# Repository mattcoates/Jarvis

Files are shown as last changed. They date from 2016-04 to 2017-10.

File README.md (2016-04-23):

#Jarvis Flight Computer & Ground Station

Jarvis is a generic rocket flight computer and ground station for use in my level 1 & 2 certification attempt rockets.

Flight Computer Specifications:
- Size: 30mm x 55mm
- Processor: STM32F411CEU6
- Power Supply: x1 Energizer L91 (AA) w/ Boost Coverter to 3.3v
- Barometer: MS5611
- Pyro Channels: x3 w/ Fire & Sense Functioniality
- Storage: S25FL127S 16MB Flash Memory
- IMU: MPU9250
- GPS: uBlox MAX-M8Q w/ PCB Mount Helical Antenna
- Telemetry: Si4460 Radio Downlink w/ SMA Connector

Ground Station Specifications:
- Size: 16mm x 44mm Dongle
- Processor: STM32F042F6P6
- Power Supply: USB with ADP3335 Regulator
- Telemetry: Si4460 Radio Downlink w/ SMA Connector
- Connectors: USB-A Male Plug

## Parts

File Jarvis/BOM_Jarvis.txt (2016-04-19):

Bill Of Materials
=================

Source file: Jarvis.xml
Date: 2016-04-19T19:52:06.596366

Parts Missing Footprints
------------------------
X1     434MHz ANT     
X5     ARM Switch     
X2     Red LED        
X4     AA Holder      
X3     AA Battery     
X8     Housing x1     
X9     Housing x4     
X10    Housing x1     
X13    F Crimps x17   
X6     Wire           
X14    Crimp Tool     
X12    M Crimps x6    
X7     Heat Shrink    
X11    Housing x3     
X16    RF Cover       

Parts Missing Order Codes
-------------------------
P3     SWD_TC          agg:TC2030-NL
X13    F Crimps x17    None
X6     Wire            None
X12    M Crimps x6     None
X7     Heat Shrink     None
TP19   TESTPAD         agg:TESTPAD
TP15   TESTPAD         agg:TESTPAD
TP6    TESTPAD         agg:TESTPAD
TP11   TESTPAD         agg:TESTPAD
TP4    TESTPAD         agg:TESTPAD
TP10   TESTPAD         agg:TESTPAD
TP12   TESTPAD         agg:TESTPAD
TP7    TESTPAD         agg:TESTPAD
TP1    TESTPAD         agg:TESTPAD
TP16   TESTPAD         agg:TESTPAD
TP14   TESTPAD         agg:TESTPAD
TP9    TESTPAD         agg:TESTPAD
TP3    TESTPAD         agg:TESTPAD
TP18   TESTPAD         agg:TESTPAD
TP13   TESTPAD         agg:TESTPAD
TP8    TESTPAD         agg:TESTPAD
TP2    TESTPAD         agg:TESTPAD
TP17   TESTPAD         agg:TESTPAD
TP26   TESTPAD         agg:TESTPAD
TP25   TESTPAD         agg:TESTPAD
TP24   TESTPAD         agg:TESTPAD
TP20   TESTPAD         agg:TESTPAD
TP21   TESTPAD         agg:TESTPAD
TP22   TESTPAD         agg:TESTPAD
TP38   TESTPAD         agg:TESTPAD
TP40   TESTPAD         agg:TESTPAD
TP33   TESTPAD         agg:TESTPAD
TP37   TESTPAD         agg:TESTPAD
TP39   TESTPAD         agg:TESTPAD
TP36   TESTPAD         agg:TESTPAD
TP44   TESTPAD         agg:TESTPAD
TP45   TESTPAD         agg:TESTPAD
TP41   TESTPAD         agg:TESTPAD
TP42   TESTPAD         agg:TESTPAD
TP47   TESTPAD         agg:TESTPAD
TP48   TESTPAD         agg:TESTPAD
TP43   TESTPAD         agg:TESTPAD
TP23   TESTPAD         agg:TESTPAD
TP32   TESTPAD         agg:TESTPAD
TP30   TESTPAD         agg:TESTPAD
TP31   TESTPAD         agg:TESTPAD
TP28   TESTPAD         agg:TESTPAD
TP27   TESTPAD         agg:TESTPAD
TP29   TESTPAD         agg:TESTPAD
TP35   TESTPAD         agg:TESTPAD
TP46   TESTPAD         agg:TESTPAD
TP34   TESTPAD         agg:TESTPAD
TP5    TESTPAD         agg:TESTPAD
TP49   TESTPAD         agg:TESTPAD

Inconsistent Order Codes
------------------------

Vendor Specific BOMs
--------------------
  RS
  ~~
883-7942,1,,1x--MPU-9250--QFN-24-MPU9250--IC3

  Digikey
  ~~~~~~~
1,AI-1027-TWT-3V-R,1x SOUNDER AI-1027-TWT-3V-R LS1

  Farnell
  ~~~~~~~
2524673,1,1x 10nF 0402-L
2346896,1,1x 2.2uF 0603-L
2455292,1,1x 2.2uH Neosid_Inductor_SM-NE
2310320,2,2x 8.2pF 0402-L
1760988,2,2x 18nH 0402-L
2497715,1,1x RF Frame BMI-S-201-F
2497714,1,1x RF Cover None
1226390,1,1x LED 0603-LED
1830730,1,1x Housing x1 None
2072516,5,5x 1k 0402-L
2072517,16,16x 10k 0402-L
1568023,1,1x MICROUSB MICROUSB_MOLEX_475
1830751,1,1x PYRO S06B-PASK-2
1515785 ,2,2x 1.25R 0402-L
2254940,1,1x ADP1607 LFCSP-2x2
2496792,1,1x 100pF 0402-L
2112849,1,1x 1uF 0603-L
1669639,3,3x 56nH 0402-L
1510761 ,4,4x NFET SOT-23
1894738,3,3x PFET SOT-23
1759381,1,1x 1uF 0402-L
2331061,1,1x 243k 0603-L
1226372,3,3x LED 0603-LED
2293260 ,1,1x AA Holder None
1657936,2,2x 10uF 0805
1863178,1,1x Red LED None
1830747,1,1x PWR S02B-PASK-2
1828860,18,18x 100nF 0402-L
1830726,1,1x Housing x4 None
1758939,2,2x 8pF 0402-L
1830728,1,1x Housing x1 None
1973025,1,1x 15pF 0402-L
1830748,1,1x ARM S03B-PASK-2
1608592,1,1x SMA SMA-142-0701-801
2362662,1,1x MS5611-01BA03 MS5611
1885342,1,1x 18pF 0402-L
2462635,1,1x Si4460 QFN-20-EP-SI
1469661,1,1x 0R 0402-L
1830756 ,1,1x Housing x3 None
2328003,1,1x S25FL127S WND008
2506973,1,1x 30MHz XTAL-20x16
2496800,1,1x 220pF 0402-L
1358015,10,10x 100R 0402-L
2456965,1,1x STM32F411CxUx QFN-48-EP-ST
1885321,1,1x 5.1pF 0402-L
2506952,1,1x 26MHz XTAL-20x16
2426952,2,2x 4.7uF 0402-L
2368169,8,8x ESD_DIODE 0402-L
2310308,1,1x 2.7pF 0402-L
2215631,1,1x 220nH 0603-L
1735379,1,1x ARM Switch None
2483918 ,1,1x 330k 0603-L

  eBay
  ~~~~
http://tinyurl.com/zxwhzow,1,1x X3 None
http://tinyurl.com/jokv8kj,1,1x X14 None

  HabSupplies
  ~~~~~~~~~~~
HAB-434STUB,1,1x X1 None
HAB-MAX-M8Q,1,1x IC2 MAX-7Q
HAB-SL1252R,1,1x P1 SMA-142-0701-801

Assembly BOM
------------
883-7942             1   MPU-9250        QFN-24-MPU9250  IC3
AI-1027-TWT-3V-R     1   SOUNDER         AI-1027-TWT-3V-R LS1
2524673              1   10nF            0402-L          C11
2346896              1   2.2uF           0603-L          C32
2455292              1   2.2uH           Neosid_Inductor_SM-NE29_SMD1008 L1
2310320              2   8.2pF           0402-L          C26 C28
1760988              2   18nH            0402-L          L4 L5
2497715              1   RF Frame        BMI-S-201-F     X15
2497714              1   RF Cover        None            X16
1226390              1   LED             0603-LED        D4
1830730              1   Housing x1      None            X10
2072516              5   1k              0402-L          R21 R22 R23 R24 R25
2072517              16  10k             0402-L          R1 R12 R13 R14 R15 R16 R17 R18 R19 R2 R20 R27 R28 R3 R35 R36
1568023              1   MICROUSB        MICROUSB_MOLEX_47589-0001 J4
1830751              1   PYRO            S06B-PASK-2     J1
1515785              2   1.25R           0402-L          FB1 FB2
2254940              1   ADP1607         LFCSP-2x2       IC1
2496792              1   100pF           0402-L          C35
2112849              1   1uF             0603-L          C33
1669639              3   56nH            0402-L          L2 L3 L6
1510761              4   NFET            SOT-23          Q4 Q5 Q6 Q7
1894738              3   PFET            SOT-23          Q1 Q2 Q3
1759381              1   1uF             0402-L          C16
2331061              1   243k            0603-L          R11
1226372              3   LED             0603-LED        D1 D2 D3
2293260              1   AA Holder       None            X4
1657936              2   10uF            0805            C2 C3
1863178              1   Red LED         None            X2
1830747              1   PWR             S02B-PASK-2     J2
1828860              18  100nF           0402-L          C1 C10 C12 C13 C14 C15 C17 C20 C29 C30 C31 C34 C37 C4 C5 C6 C8 C9
1830726              1   Housing x4      None            X9
1758939              2   8pF             0402-L          C21 C22
1830728              1   Housing x1      None            X8
1973025              1   15pF            0402-L          C27
1830748              1   ARM             S03B-PASK-2     J3
1608592              1   SMA             SMA-142-0701-801 P2
2362662              1   MS5611-01BA03   MS5611          IC6
1885342              1   18pF            0402-L          C25
2462635              1   Si4460          QFN-20-EP-SI    IC5
1469661              1   0R              0402-L          R32
1830756              1   Housing x3      None            X11
2328003              1   S25FL127S       WND008          IC7
2506973              1   30MHz           XTAL-20x16      Y2
2496800              1   220pF           0402-L          C36
1358015              10  100R            0402-L          R10 R26 R29 R33 R34 R4 R5 R6 R8 R9
2456965              1   STM32F411CxUx   QFN-48-EP-ST    IC4
1885321              1   5.1pF           0402-L          C23
2506952              1   26MHz           XTAL-20x16      Y1
2426952              2   4.7uF           0402-L          C19 C7
2368169              8   ESD_DIODE       0402-L          D10 D11 D12 D5 D6 D7 D8 D9
2310308              1   2.7pF           0402-L          C24
2215631              1   220nH           0603-L          L7
1735379              1   ARM Switch      None            X5
2483918              1   330k            0603-L          R7
http://tinyurl.com/zxwhzow 1   AA Battery      None            X3
http://tinyurl.com/jokv8kj 1   Crimp Tool      None            X14
HAB-434STUB          1   434MHz ANT      None            X1
HAB-MAX-M8Q          1   MAX-8Q          MAX-7Q          IC2
HAB-SL1252R          1   SMA             SMA-142-0701-801 P1

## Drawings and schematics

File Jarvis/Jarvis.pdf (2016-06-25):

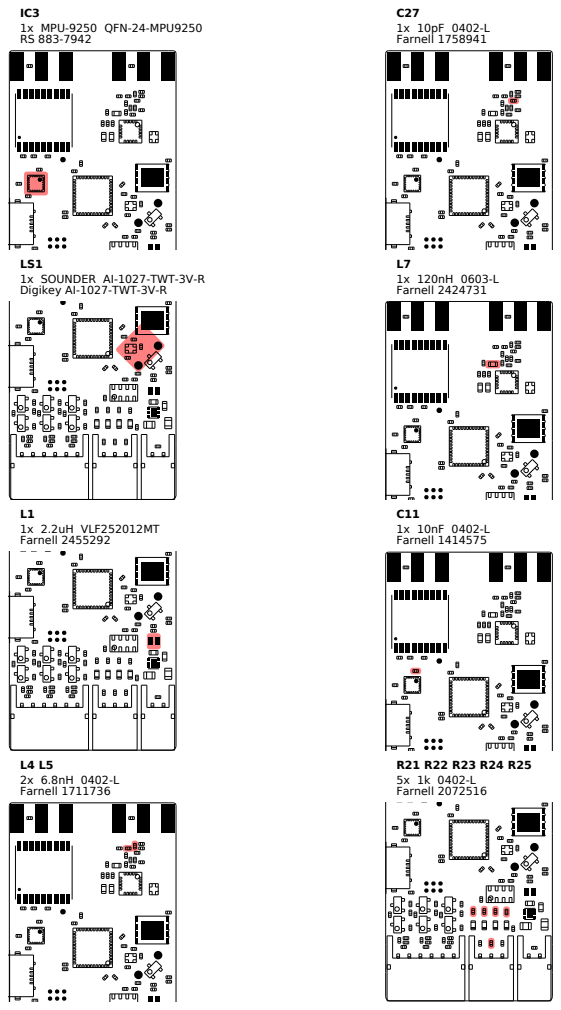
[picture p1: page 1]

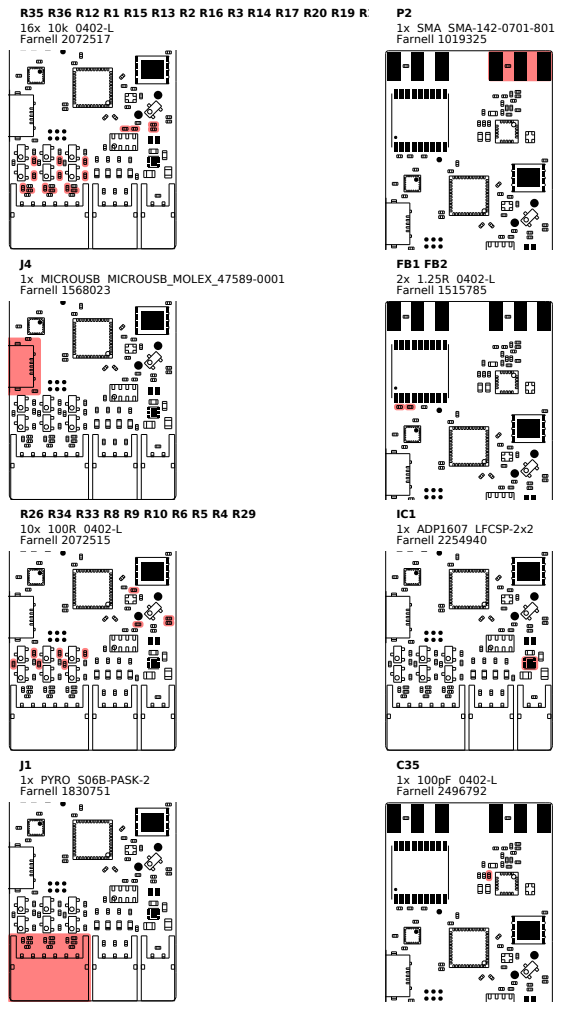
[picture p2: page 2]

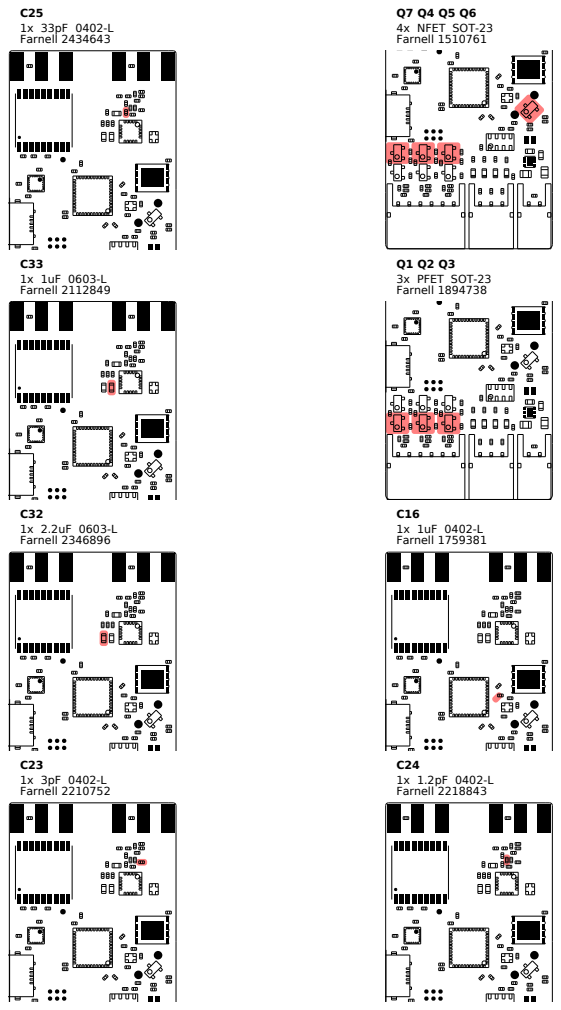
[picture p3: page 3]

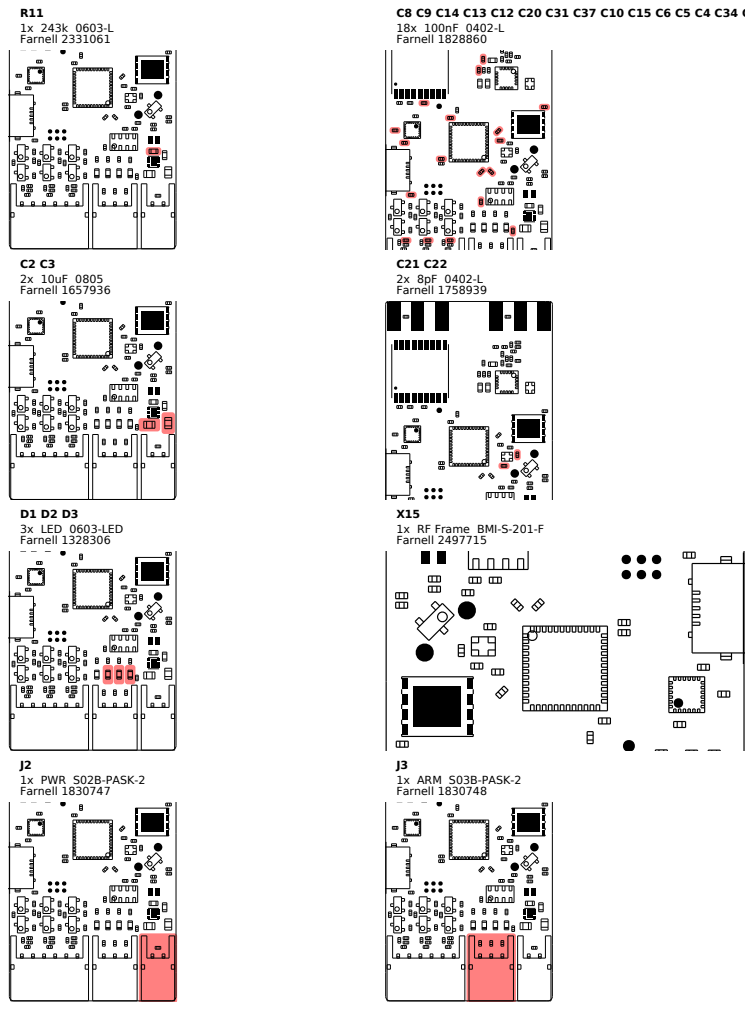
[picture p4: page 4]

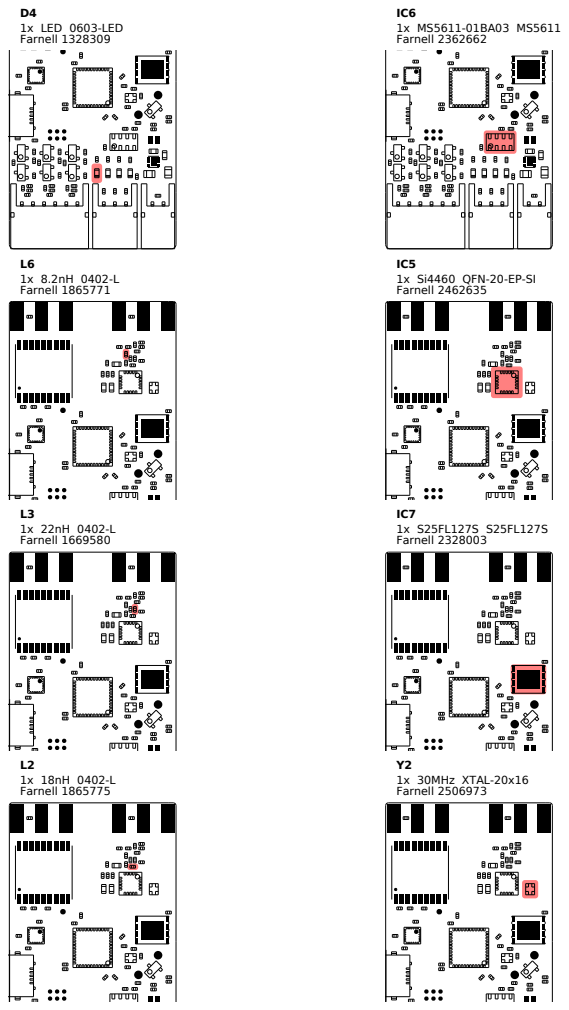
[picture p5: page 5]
D4 1x LED 0603-LED; L6 1x 8.2nH 0402-L Farnell 1865771; L3 1x 22nH 0402-L Farnell 1669580; L2 1x 18nH 0402-L Farnell 1865775; IC5 1x Si4460 QFN-20-EP-SI Farnell 2462635; IC7 1x S25FL127S S25FL127S Farnell 2328003; Y2 1x 30MHz XTAL-20x16 Farnell 2506973

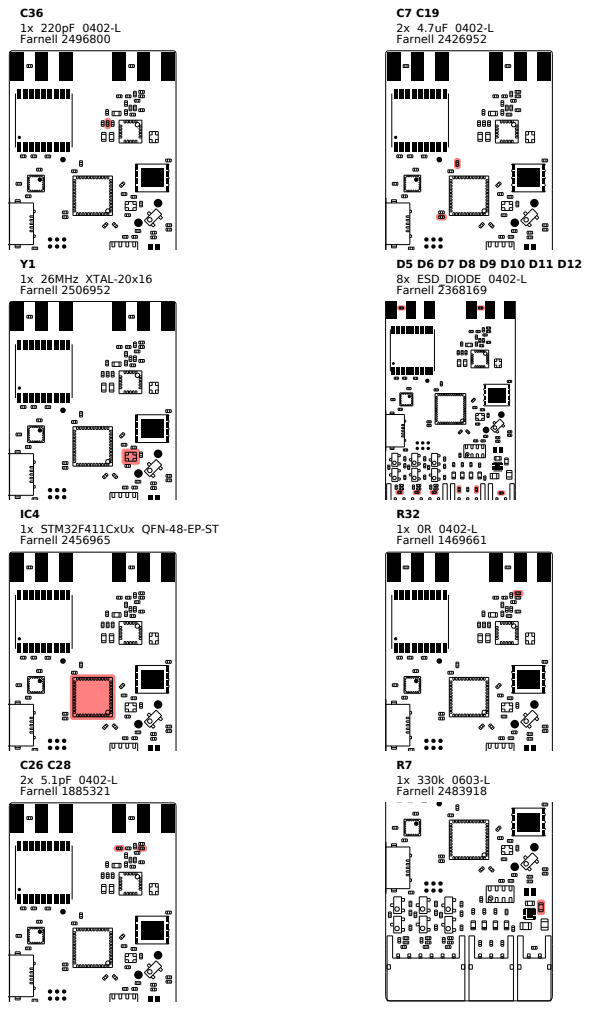
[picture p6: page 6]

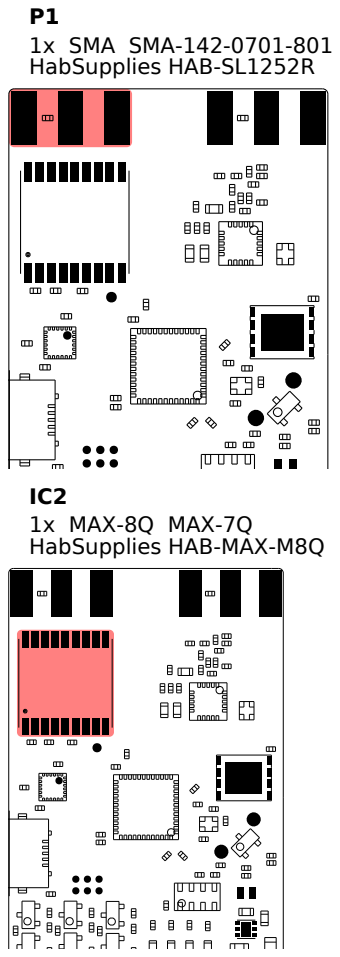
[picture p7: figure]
P1 1x SMA SMA-142-0701-801 HabSupplies HAB-SL1252R; IC2 1x MAX-8Q MAX-7Q HabSupplies HAB-MAX-M8Q

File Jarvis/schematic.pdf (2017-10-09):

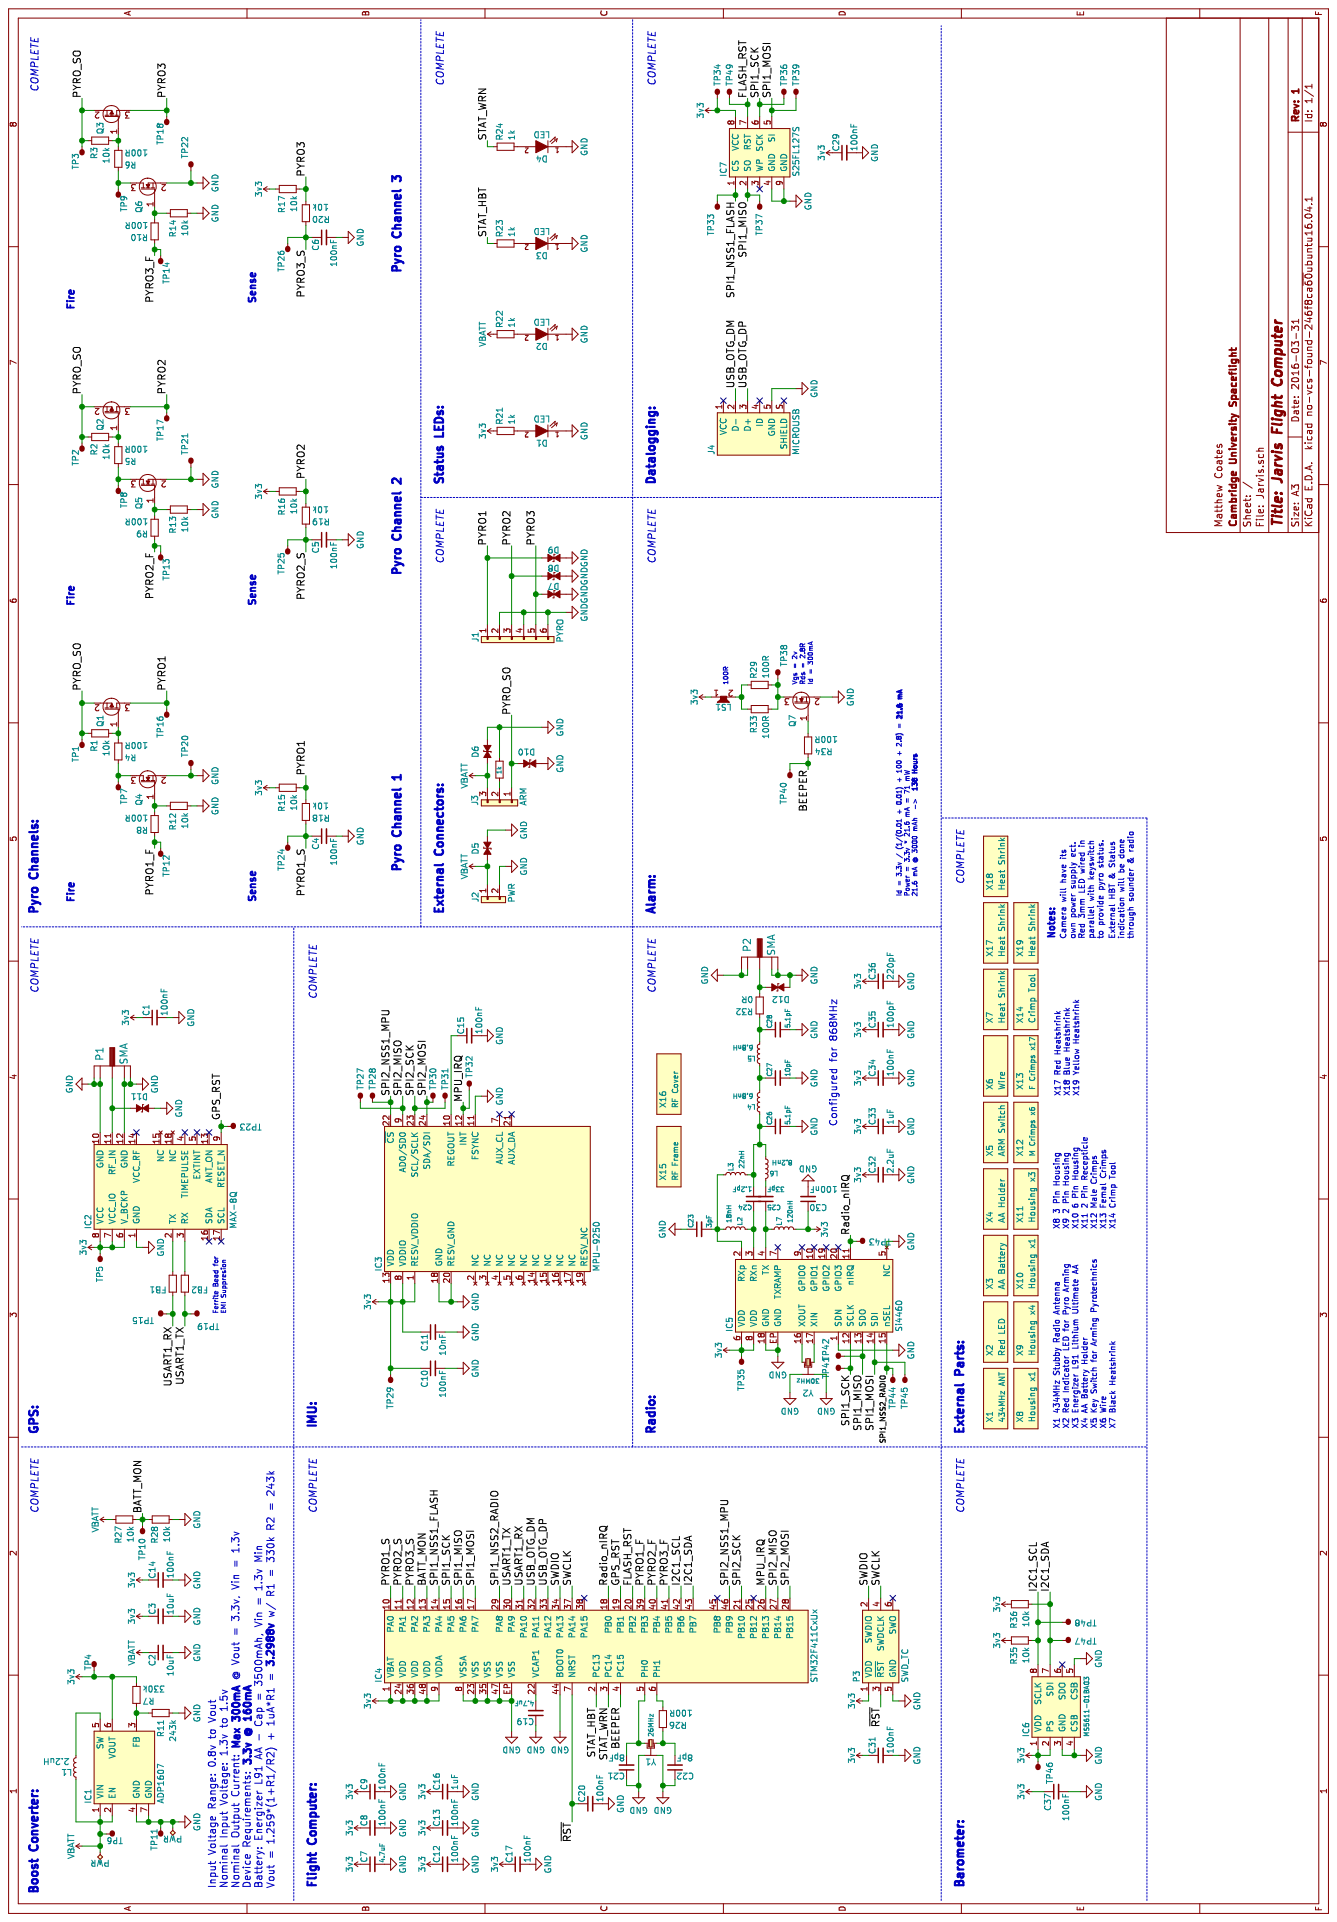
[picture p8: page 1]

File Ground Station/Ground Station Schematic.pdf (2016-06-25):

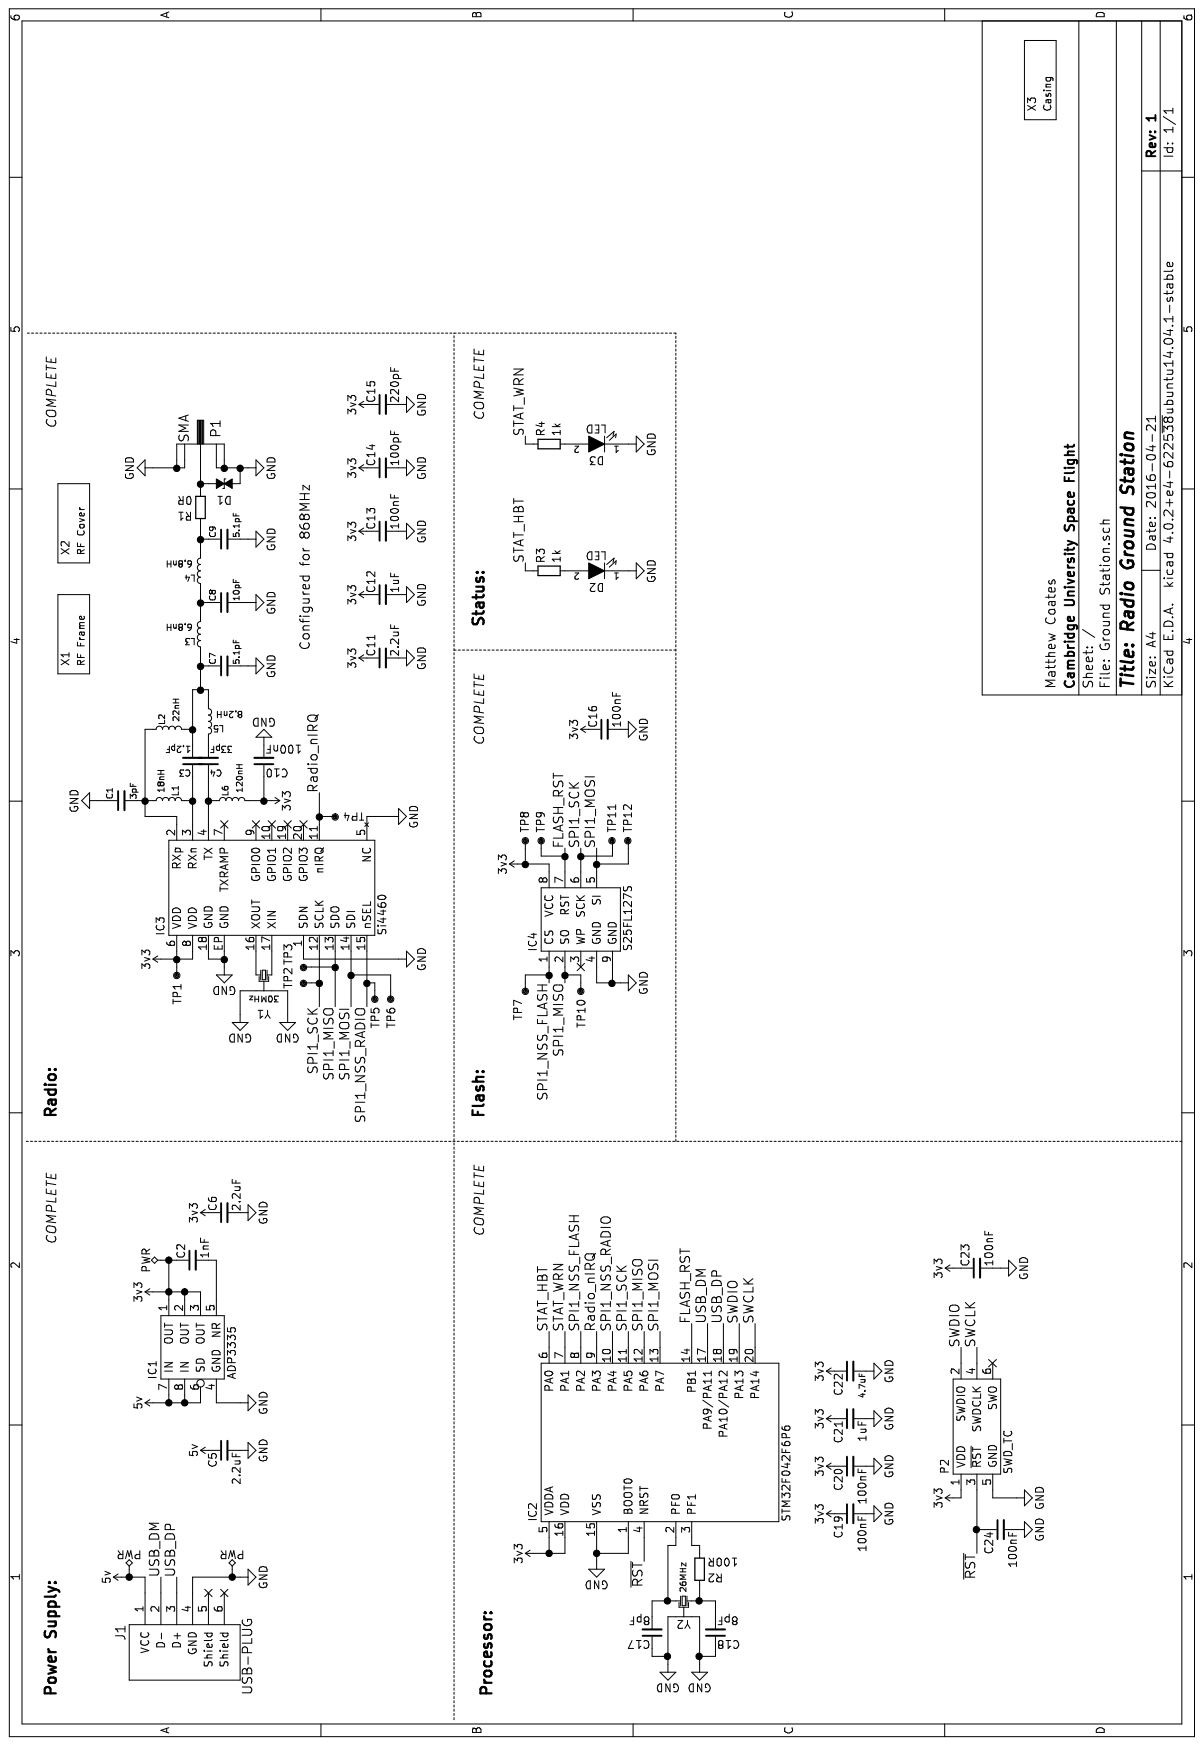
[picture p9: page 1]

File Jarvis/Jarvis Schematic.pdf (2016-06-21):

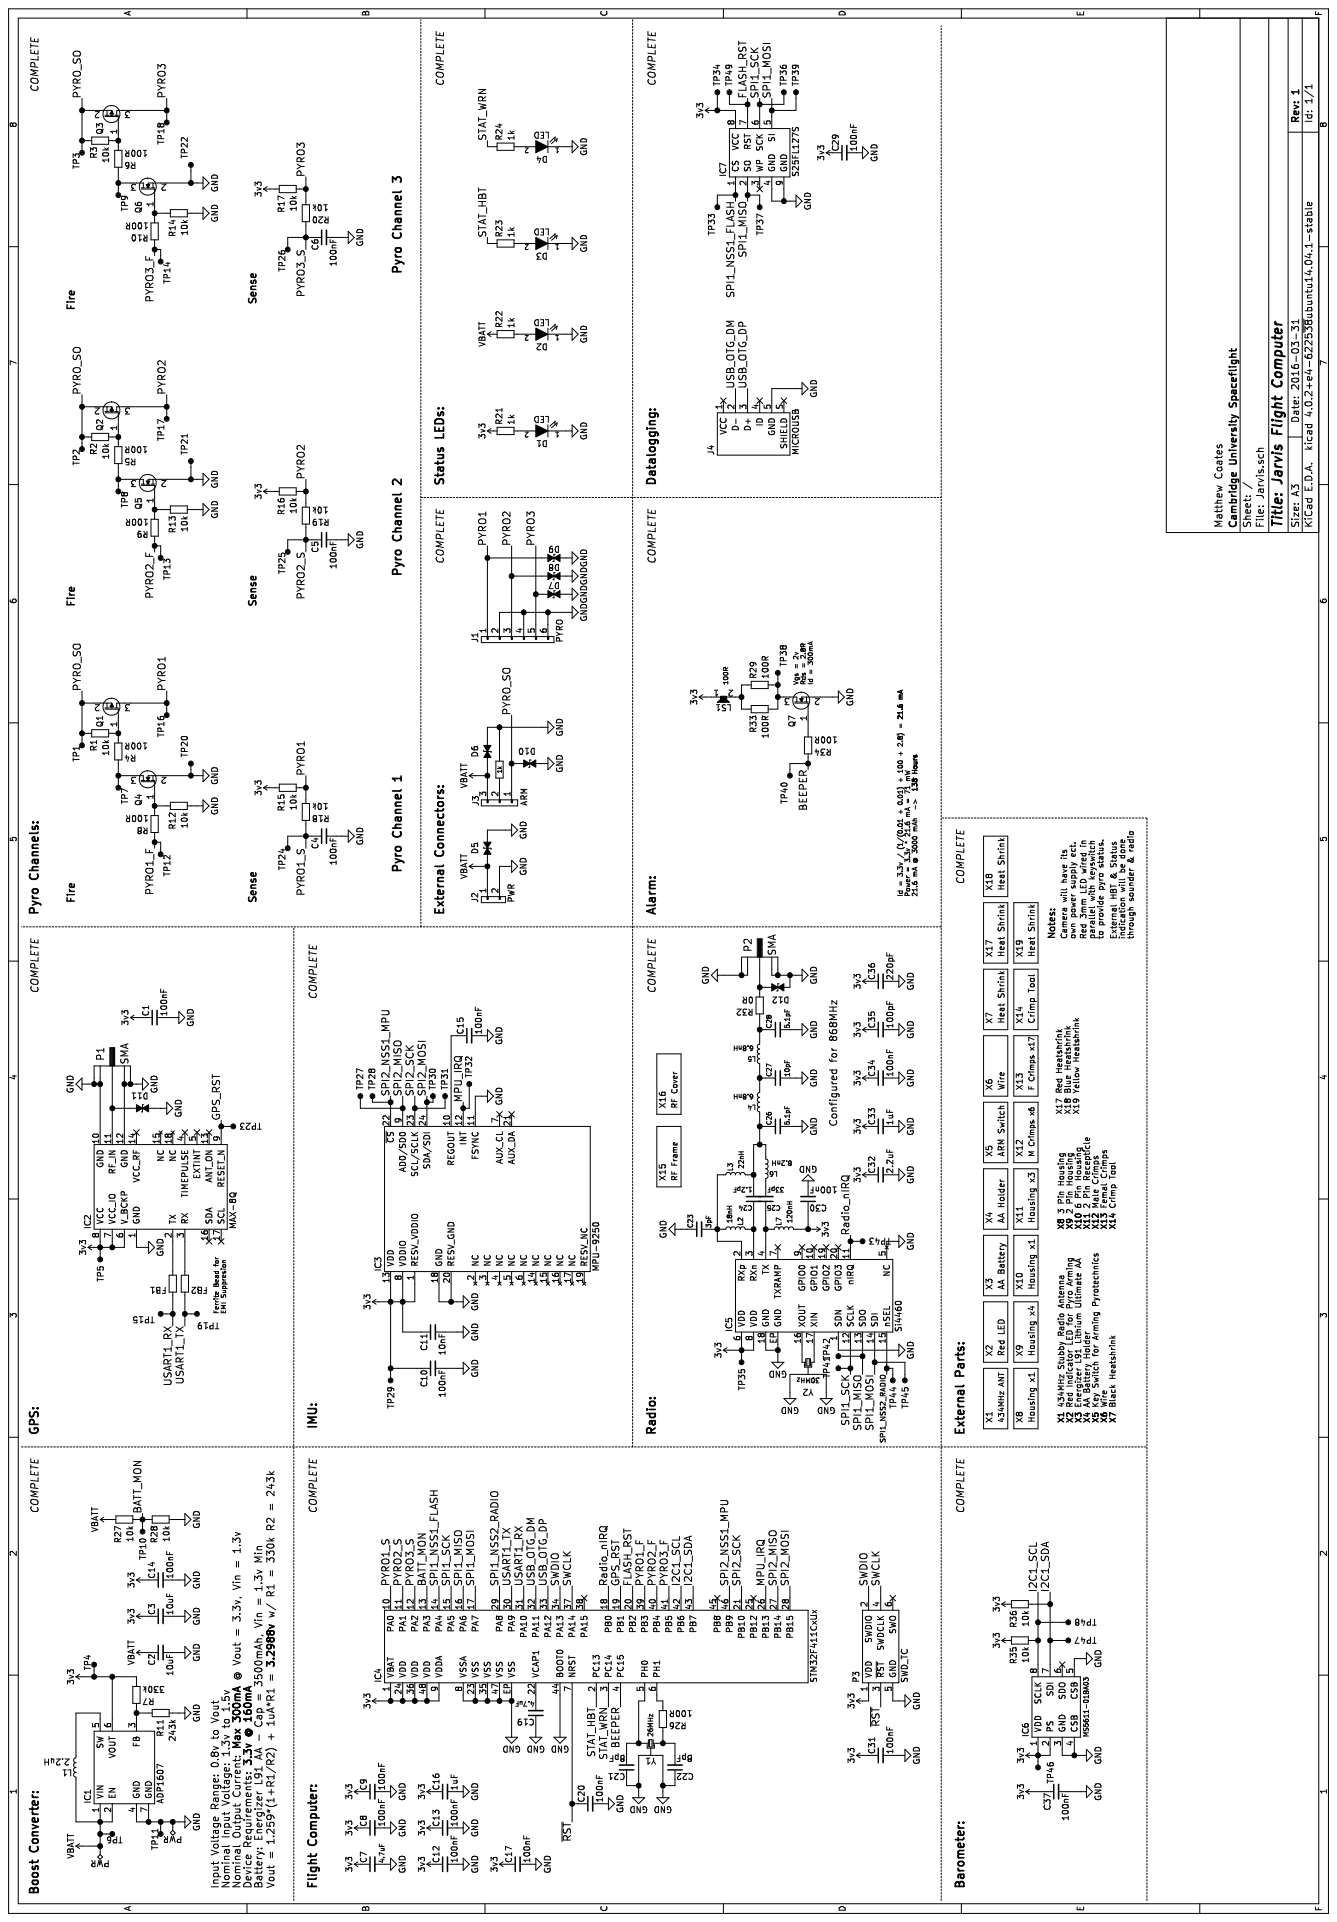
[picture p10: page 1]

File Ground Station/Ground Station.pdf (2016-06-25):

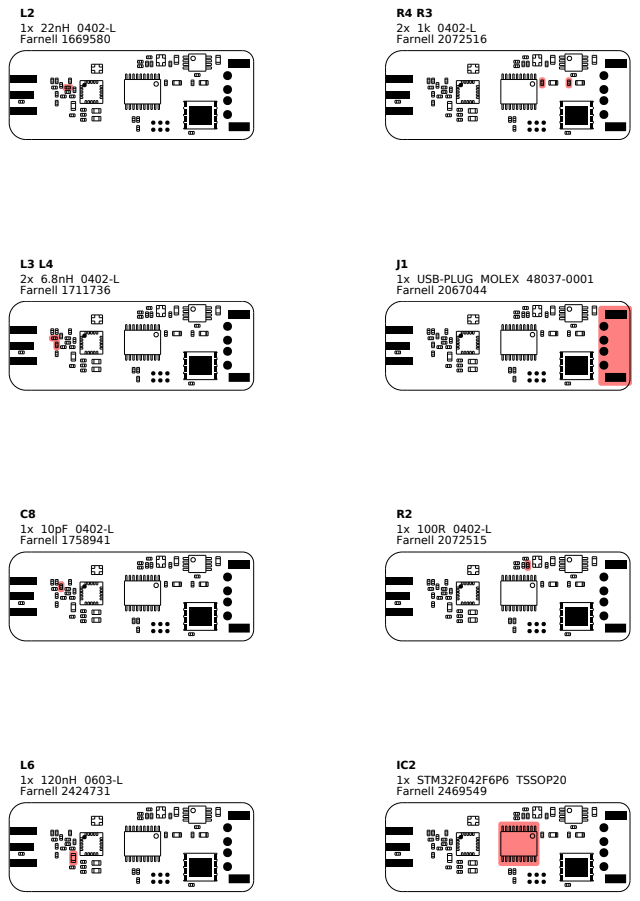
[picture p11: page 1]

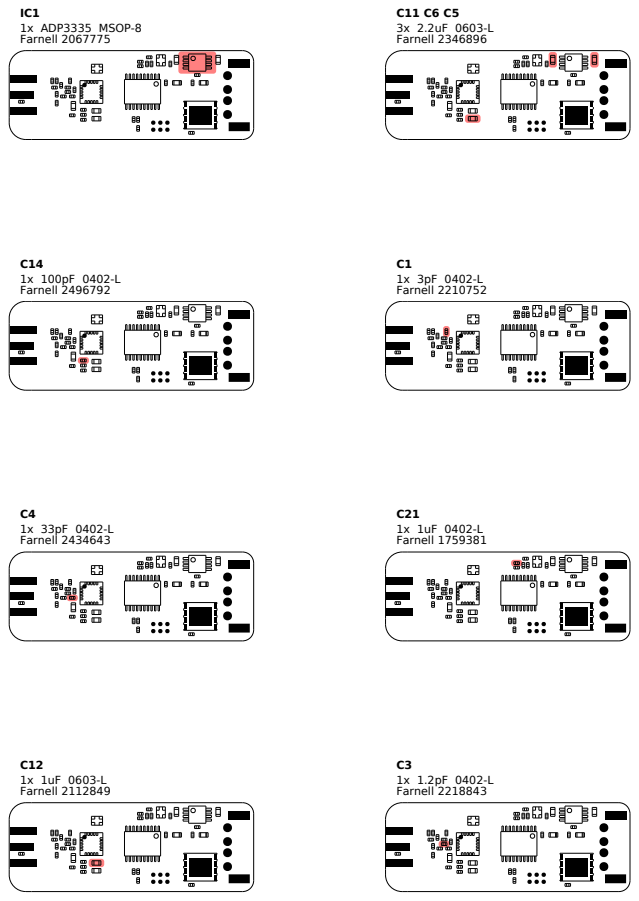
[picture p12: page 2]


Y1 1x 30MHz XTAL-20x16 Farnell 2506973; C15 1x 220pF 0402-L Farnell 2496800; Y2 1x 26MHz XTAL-20x16 Farnell 2506952; C2 1x 1nF 0402-L Farnell 1535558; C22 1x 4.7uF 0402-L Farnell 2426952; D1 1x ESD_DIODE 0402-L Farnell 2368169

R1
1x 0R 0402-L

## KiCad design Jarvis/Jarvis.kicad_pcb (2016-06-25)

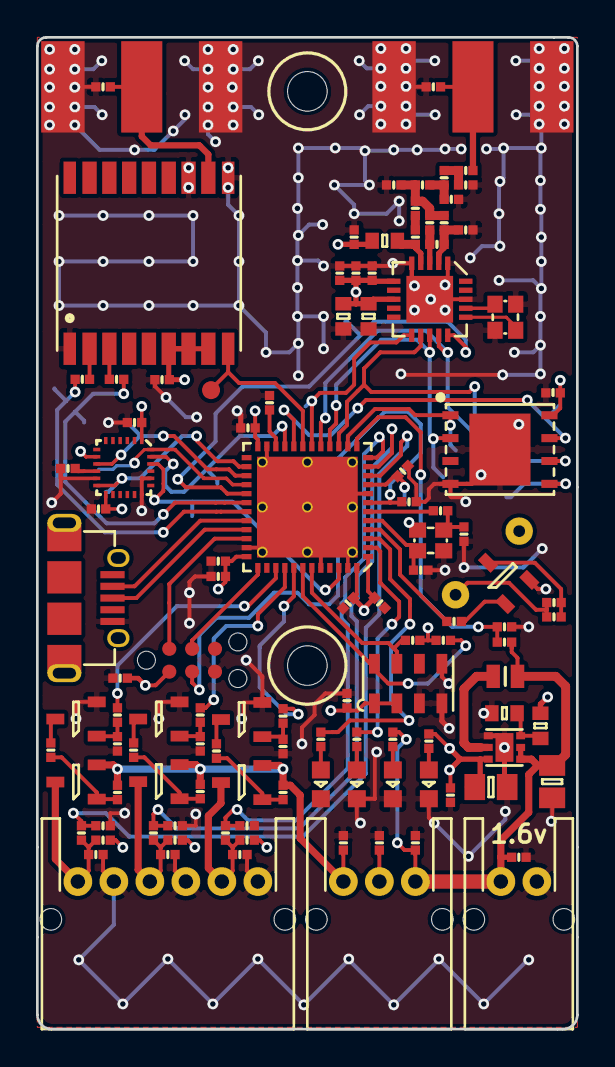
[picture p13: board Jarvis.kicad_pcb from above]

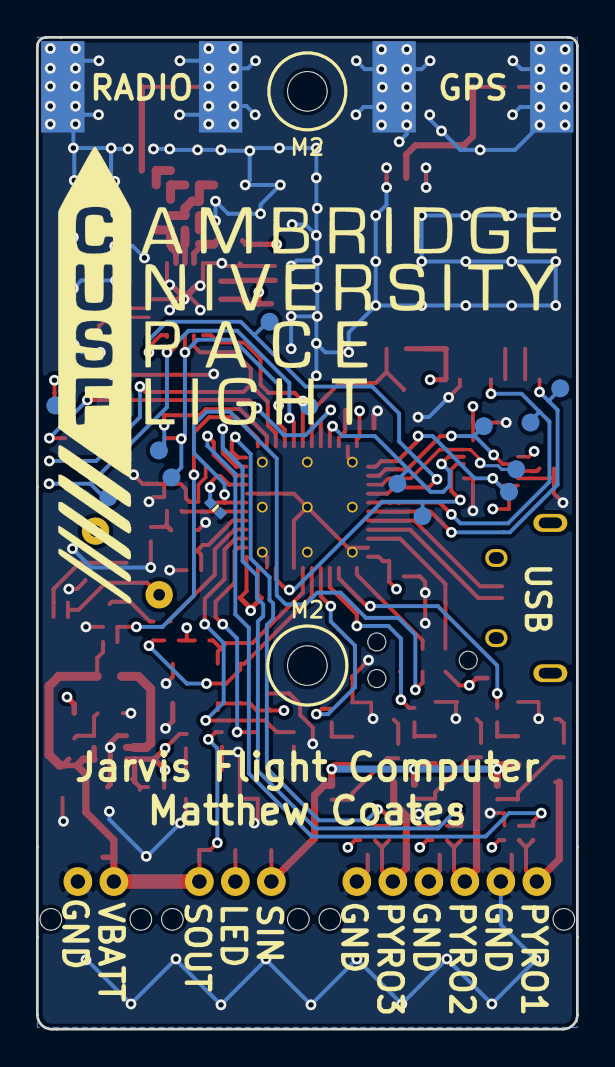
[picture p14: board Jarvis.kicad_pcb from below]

Board: 4 copper layers, 30.0 x 55.1 mm, 130 parts (16 on the bottom side), 76 nets.

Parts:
C1, C4, C5, C6, C8, C9, C10, C12, C13, C14, C15, C17, C20, C29, C30, C31, C34, C37: 100nF; 0402-L
C2, C3: 10uF; 0805
C7, C19: 4.7uF; 0402-L
C11: 10nF; 0402-L
C16: 1uF; 0402-L
C21, C22: 8pF; 0402-L
C23: 3pF; 0402-L
C24: 1.2pF; 0402-L
C25: 33pF; 0402-L
C26, C28: 5.1pF; 0402-L
C27: 10pF; 0402-L
C32: 2.2uF; 0603-L
C33: 1uF; 0603-L
C35: 100pF; 0402-L
C36: 220pF; 0402-L
D1, D2, D3, D4: LED; 0603-LED
D5, D6, D7, D8, D9, D10, D11, D12: ESD_DIODE; 0402-L
FB1, FB2: 1.25R; 0402-L
IC1: ADP1607; LFCSP-2x2
IC2: MAX-8Q; MAX-7Q
IC3: MPU-9250; QFN-24-MPU9250
IC4: STM32F411CxUx; QFN-48-EP-ST
IC5: Si4460; QFN-20-EP-SI
IC6: MS5611-01BA03; MS5611
IC7: S25FL127S
J1: PYRO; S06B-PASK-2
J2: PWR; S02B-PASK-2
J3: ARM; S03B-PASK-2
J4: MICROUSB; MICROUSB_MOLEX_47589-0001
L1: 2.2uH; VLF252012MT
L2: 18nH; 0402-L
L3: 22nH; 0402-L
L4, L5: 6.8nH; 0402-L
L6: 8.2nH; 0402-L
L7: 120nH; 0603-L
LS1: SOUNDER; AI-1027-TWT-3V-R
P1, P2: SMA; SMA-142-0701-801
P3: SWD_TC; TC2030-NL
Q1, Q2, Q3: PFET; SOT-23
Q4, Q5, Q6, Q7: NFET; SOT-23
R1, R2, R3, R12, R13, R14, R15, R16, R17, R18, R19, R20, R27, R28, R35, R36: 10k; 0402-L
R4, R5, R6, R8, R9, R10, R26, R29, R33, R34: 100R; 0402-L
R7: 330k; 0603-L
R11: 243k; 0603-L
R21, R22, R23, R24, R25: 1k; 0402-L
R32: 0R; 0402-L
TP15, TP19, TP23, TP27, TP28, TP30, TP31, TP32, TP33, TP36, TP37, TP39, TP43, TP44, TP49: TESTPAD
Y1: 26MHz; XTAL-20x16
Y2: 30MHz; XTAL-20x16

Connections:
3v3: C1.1, C3.1, C7.1, C8.1, C9.1, C10.1, C11.1, C12.1, C13.1, C14.1, C16.1, C17.1, C29.1, C30.1, C31.1, C32.1, C33.1, C34.1, C35.1, C36.1, C37.1, IC1.6, IC2.6, IC2.7, IC2.8, IC3.1, IC3.8, IC3.13, IC4.1, IC4.9, IC4.24, IC4.36, IC4.48, IC5.6, IC5.8, IC6.1, IC6.2, IC7.8, L7.2, LS1.1, P3.1, R7.2, R15.1, R16.1, R17.1, R21.1, R35.1, R36.1
/BATT_MON: IC4.13, R27.2, R28.1
/BEEPER: IC4.4, R34.1
/FLASH_RST: IC4.20, IC7.7, TP49.1
/GPS_RST: IC2.9, IC4.19, TP23.1
/I2C1_SCL: IC4.42, IC6.8, R35.2
/I2C1_SDA: IC4.43, IC6.7, R36.2
/MPU_IRQ: IC3.12, IC4.26, TP32.1
/PYRO1: D9.2, J1.1, Q1.3, R15.2, R18.2
/PYRO1_F: IC4.39, R8.1
/PYRO1_S: C4.1, IC4.10, R18.1
/PYRO2: D8.2, J1.3, Q2.3, R16.2, R19.2
/PYRO2_F: IC4.40, R9.1
/PYRO2_S: C5.1, IC4.11, R19.1
/PYRO3: D7.2, J1.5, Q3.3, R17.2, R20.2
/PYRO3_F: IC4.41, R10.1
/PYRO3_S: C6.1, IC4.12, R20.1
/PYRO_SO: D10.2, J3.1, Q1.2, Q2.2, Q3.2, R1.1, R2.1, R3.1
/Radio_nIRQ: IC4.18, IC5.11, TP43.1
/SPI1_MISO: IC4.16, IC5.13, IC7.2, TP37.1
/SPI1_MOSI: IC4.17, IC5.14, IC7.5, TP39.1
/SPI1_NSS1_FLASH: IC4.14, IC7.1, TP33.1
/SPI1_NSS2_RADIO: IC4.29, IC5.15, TP44.1
/SPI1_SCK: IC4.15, IC5.12, IC7.6, TP36.1
/SPI2_MISO: IC3.9, IC4.27, TP27.1
/SPI2_MOSI: IC3.24, IC4.28, TP30.1
/SPI2_NSS1_MPU: IC3.22, IC4.46, TP28.1
/SPI2_SCK: IC3.23, IC4.21, TP31.1
/STAT_HBT: IC4.2, R23.1
/STAT_WRN: IC4.3, R24.1
/SWCLK: IC4.37, P3.4
/SWDIO: IC4.34, P3.2
/USART1_RX: FB1.1, IC4.31, TP15.1
/USART1_TX: FB2.1, IC4.30, TP19.1
/USB_OTG_DM: IC4.32, J4.2
/USB_OTG_DP: IC4.33, J4.3
/~RST: C20.1, IC4.7, P3.3
GND: C1.2, C2.2, C3.2, C4.2, C5.2, C6.2, C7.2, C8.2, C9.2, C10.2, C11.2, C12.2, C13.2, C14.2, C15.2, C16.2, C17.2, C19.1, C20.2, C21.1, C22.1, C23.1, C26.2, C27.2, C28.2, C29.2, C30.2, C31.2, C32.2, C33.2, C34.2, C35.2, C36.2, C37.2, D1.1, D2.1, D3.1, D4.1, D5.1, D6.1, D7.1, D8.1, D9.1, D10.1, D11.1, D12.2, IC1.4, IC1.7, IC2.1, IC2.10, IC2.12, IC3.11, IC3.18, IC3.20, IC4.8, IC4.23, IC4.35, IC4.44, IC4.47, IC4.EP, IC5.1, IC5.5, IC5.18, IC5.EP, IC6.3, IC6.4, IC6.5, IC7.4, IC7.9, J1.2, J1.4, J1.6, J2.2, J4.5, P1.2, P1.3, P1.4, P1.5, P2.2, P2.3, P2.4, P2.5, P3.5, Q4.2, Q5.2, Q6.2, Q7.2, R11.2, R12.2, R13.2, R14.2, R25.2, R28.2, Y1.2, Y1.4, Y2.2, Y2.4
unnamed: C15.1, IC3.10
unnamed: C19.2, IC4.22
unnamed: C21.2, IC4.5, Y1.1
unnamed: C22.2, R26.1, Y1.3
unnamed: C23.2, IC5.2, L2.2, L3.1
unnamed: C24.1, IC5.3, L2.1
unnamed: C24.2, C26.1, L3.2, L4.1, L6.2
unnamed: C25.1, IC5.4, L7.1
unnamed: C25.2, L6.1
unnamed: C27.1, L4.2, L5.1
unnamed: C28.1, L5.2, R32.1
unnamed: D1.2, R21.2
unnamed: D2.2, R22.2
unnamed: D3.2, R23.2
unnamed: D4.2, R24.2
unnamed: D11.2, IC2.11, P1.1
unnamed: D12.1, P2.1, R32.2
unnamed: FB1.2, IC2.2
unnamed: FB2.2, IC2.3
unnamed: IC1.3, R7.1, R11.1
unnamed: IC1.5, L1.2
unnamed: IC4.6, R26.2
unnamed: IC5.16, Y2.1
unnamed: IC5.17, Y2.3
unnamed: J3.2, R25.1
unnamed: LS1.2, R29.1, R33.1
unnamed: Q1.1, R1.2, R4.2
unnamed: Q2.1, R2.2, R5.2
unnamed: Q3.1, R3.2, R6.2
unnamed: Q4.1, R8.2, R12.1
unnamed: Q4.3, R4.1
unnamed: Q5.1, R9.2, R13.1
unnamed: Q5.3, R5.1
unnamed: Q6.1, R10.2, R14.1
unnamed: Q6.3, R6.1
unnamed: Q7.1, R34.2
unnamed: Q7.3, R29.2, R33.2
VBATT: C2.1, D5.2, D6.2, IC1.1, IC1.2, J2.1, J3.3, L1.1, R22.1, R27.1

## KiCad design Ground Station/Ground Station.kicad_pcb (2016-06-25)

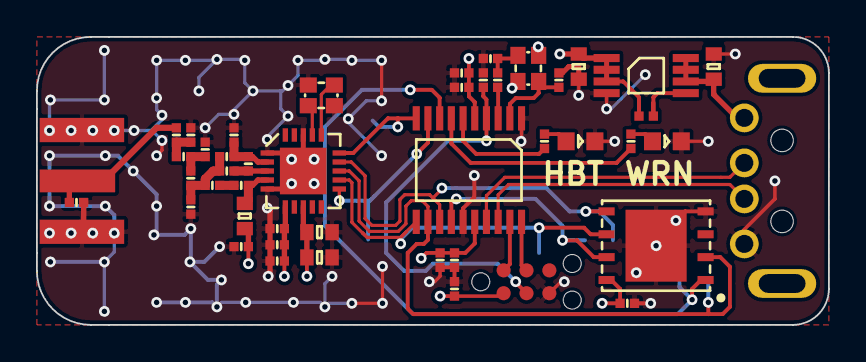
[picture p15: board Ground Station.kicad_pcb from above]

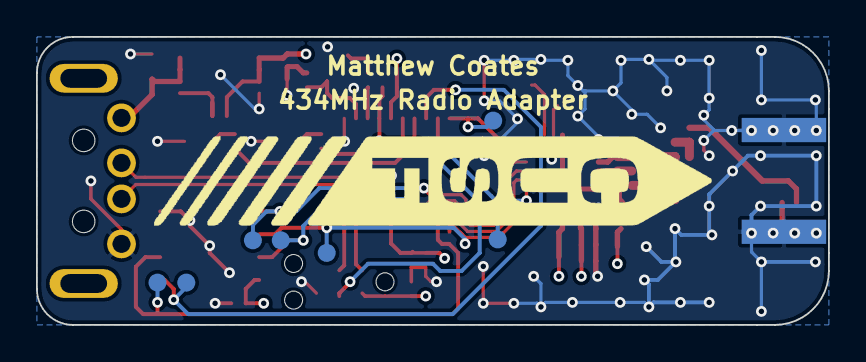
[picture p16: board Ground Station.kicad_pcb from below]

Board: 4 copper layers, 44.0 x 16.0 mm, 54 parts (7 on the bottom side), 33 nets.

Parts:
C1: 3pF; 0402-L
C2: 1nF; 0402-L
C3: 1.2pF; 0402-L
C4: 33pF; 0402-L
C5, C6, C11: 2.2uF; 0603-L
C7, C9: 5.1pF; 0402-L
C8: 10pF; 0402-L
C10, C13, C16, C19, C20, C23, C24: 100nF; 0402-L
C12: 1uF; 0603-L
C14: 100pF; 0402-L
C15: 220pF; 0402-L
C17, C18: 8pF; 0402-L
C21: 1uF; 0402-L
C22: 4.7uF; 0402-L
D1: ESD_DIODE; 0402-L
D2, D3: LED; 0603-LED
IC1: ADP3335; MSOP-8
IC2: STM32F042F6P6; TSSOP20
IC3: Si4460; QFN-20-EP-SI
IC4: S25FL127S
J1: USB-PLUG; MOLEX 48037-0001
L1: 18nH; 0402-L
L2: 22nH; 0402-L
L3, L4: 6.8nH; 0402-L
L5: 8.2nH; 0402-L
L6: 120nH; 0603-L
P1: SMA; SMA-J-P-H-ST-EM1
P2: SWD_TC; TC2030-NL
R1: 0R; 0402-L
R2: 100R; 0402-L
R3, R4: 1k; 0402-L
TP2, TP3, TP4, TP5, TP6, TP7, TP9: TESTPAD
X1: RF Frame; BMI-S-201-F
Y1: 30MHz; XTAL-20x16
Y2: 26MHz; XTAL-20x16

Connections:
3v3: C2.1, C6.1, C10.1, C11.1, C12.1, C13.1, C14.1, C15.1, C16.1, C19.1, C20.1, C21.1, C22.1, C23.1, IC1.1, IC1.2, IC1.3, IC2.5, IC2.16, IC3.6, IC3.8, IC4.8, L6.2, P2.1
5v: C5.1, IC1.6, IC1.7, IC1.8, J1.1
/FLASH_RST: IC2.14, IC4.7, TP9.1
/Radio_nIRQ: IC2.9, IC3.11, TP4.1
/SPI1_MISO: IC2.12, IC3.13, IC4.2, TP3.1
/SPI1_MOSI: IC2.13, IC3.14, IC4.5, TP6.1
/SPI1_NSS_FLASH: IC2.8, IC4.1, TP7.1
/SPI1_NSS_RADIO: IC2.10, IC3.15, TP5.1
/SPI1_SCK: IC2.11, IC3.12, IC4.6, TP2.1
/STAT_HBT: IC2.6, R3.1
/STAT_WRN: IC2.7, R4.1
/SWCLK: IC2.20, P2.4
/SWDIO: IC2.19, P2.2
/USB_DM: IC2.17, J1.2
/USB_DP: IC2.18, J1.3
/~RST: C24.1, IC2.4, P2.3
GND: C1.1, C5.2, C6.2, C7.2, C8.2, C9.2, C10.2, C11.2, C12.2, C13.2, C14.2, C15.2, C16.2, C17.1, C18.1, C19.2, C20.2, C21.2, C22.2, C23.2, C24.2, D1.2, D2.1, D3.1, IC1.4, IC2.1, IC2.15, IC3.1, IC3.5, IC3.18, IC3.EP, IC4.4, IC4.9, J1.4, P1.2, P1.3, P1.4, P1.5, P2.5, Y1.2, Y1.4, Y2.2, Y2.4
unnamed: C1.2, IC3.2, L1.2, L2.1
unnamed: C2.2, IC1.5
unnamed: C3.1, IC3.3, L1.1
unnamed: C3.2, C7.1, L2.2, L3.1, L5.2
unnamed: C4.1, IC3.4, L6.1
unnamed: C4.2, L5.1
unnamed: C8.1, L3.2, L4.1
unnamed: C9.1, L4.2, R1.1
unnamed: C17.2, IC2.2, Y2.1
unnamed: C18.2, R2.1, Y2.3
unnamed: D1.1, P1.1, R1.2
unnamed: D2.2, R3.2
unnamed: D3.2, R4.2
unnamed: IC2.3, R2.2
unnamed: IC3.16, Y1.1
unnamed: IC3.17, Y1.3

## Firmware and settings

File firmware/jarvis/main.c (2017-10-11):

#include "ch.h"
#include "hal.h"
#include "measure.h"


/* EXT Interrupt Config */
static const EXTConfig extcfg = {
  {
    {EXT_CH_MODE_FALLING_EDGE | EXT_CH_MODE_AUTOSTART | EXT_MODE_GPIOB, NULL}, /* PB0 - Radio IRQ */
    {EXT_CH_MODE_DISABLED, NULL}, /* Px1 */
    {EXT_CH_MODE_DISABLED, NULL}, /* Px2 */
    {EXT_CH_MODE_DISABLED, NULL}, /* Px3 */
    {EXT_CH_MODE_DISABLED, NULL}, /* Px4 */
    {EXT_CH_MODE_DISABLED, NULL}, /* Px5 */
    {EXT_CH_MODE_DISABLED, NULL}, /* Px6 */
    {EXT_CH_MODE_DISABLED, NULL}, /* Px7 */
    {EXT_CH_MODE_DISABLED, NULL}, /* Px8 */
    {EXT_CH_MODE_DISABLED, NULL}, /* Px9 */
    {EXT_CH_MODE_DISABLED, NULL}, /* Px10 */
    {EXT_CH_MODE_DISABLED, NULL}, /* Px11 */
    {EXT_CH_MODE_DISABLED, NULL}, /* Px12 */
    {EXT_CH_MODE_FALLING_EDGE | EXT_CH_MODE_AUTOSTART | EXT_MODE_GPIOB, NULL}, /* PB13 - MPU9250 IRQ */
    {EXT_CH_MODE_DISABLED, NULL}, /* Px14 */
    {EXT_CH_MODE_DISABLED, NULL}, /* Px15 */
    {EXT_CH_MODE_DISABLED, NULL}, /* PVD */
    {EXT_CH_MODE_DISABLED, NULL}, /* RTC Alarm Event */
    {EXT_CH_MODE_DISABLED, NULL}, /* USB Wakeup Event */
    {EXT_CH_MODE_DISABLED, NULL}, /* RTC Tamper */
    {EXT_CH_MODE_DISABLED, NULL}, /* RTC Wakeup Event */
    {EXT_CH_MODE_DISABLED, NULL}, /* COMP1 */
    {EXT_CH_MODE_DISABLED, NULL}  /* COMP2 */
  }
};


/* Heartbeat Thread */ 
static THD_WORKING_AREA(waHBT, 128);
static THD_FUNCTION(HBT, arg) {
  
    (void)arg;
    chRegSetThreadName("heartbeat");    
    while (true) {
        
        palSetPad(GPIOC, GPIOC_STAT_HBT);
        //palSetPad(GPIOC, GPIOC_BEEP);
        chThdSleepMilliseconds(100);
        
        palClearPad(GPIOC, GPIOC_STAT_HBT);
        //palClearPad(GPIOC, GPIOC_BEEP);    
        chThdSleepMilliseconds(500);
    }
}


/* Application Entry Point */
int main(void) {

    /* Allow debug access during WFI sleep */
    DBGMCU->CR |= DBGMCU_CR_DBG_SLEEP;

    /* Initialise ChibiOS */
    halInit();
    chSysInit();
    
    /* EXT Driver Init */
    extStart(&EXTD1, &extcfg);
    
    /* Start Measurements */
    begin_measurements();

    /* Heartbeat Init */
    chThdCreateStatic(waHBT, sizeof(waHBT), NORMALPRIO, HBT, NULL);

    /* Do Nothing */
    while (true) {
    }
}

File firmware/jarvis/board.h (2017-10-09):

/*
    ChibiOS - Copyright (C) 2006..2016 Giovanni Di Sirio
    Licensed under the Apache License, Version 2.0 (the "License");
    you may not use this file except in compliance with the License.
    You may obtain a copy of the License at
    http://www.apache.org/licenses/LICENSE-2.0
    Unless required by applicable law or agreed to in writing, software
    distributed under the License is distributed on an "AS IS" BASIS,
    WITHOUT WARRANTIES OR CONDITIONS OF ANY KIND, either express or implied.
    See the License for the specific language governing permissions and
    limitations under the License.
*/

/*
    Generated by gen-board.h.py based on board.yaml
*/

#ifndef _BOARD_H_
#define _BOARD_H_


/*
    Setup for Jarvis Flight Computer
*/

/*
    Board identifier
*/
#define BOARD_JARVIS_FLIGHT_COMPUTER
#define BOARD_NAME                     "Jarvis Flight Computer"

/*
    Board oscillators-related settings.
*/
#if !defined(STM32_LSECLK)
#define STM32_LSECLK                   0U
#endif

#if !defined(STM32_HSECLK)
#define STM32_HSECLK                   26000000U
#endif

/*
    Board voltages
    Required for performance limits calculation.
*/
#define STM32_VDD                      300U

/*
    MCU type as defined in the ST header.
*/
#define STM32F411xE

/*
    IO pins assignments.
*/
#define GPIOA_PYROS_1                  0U
#define GPIOA_PYROS_2                  1U
#define GPIOA_PYROS_3                  2U
#define GPIOA_BAT_MON                  3U
#define GPIOA_FLASH_CS                 4U
#define GPIOA_SPI1_SCK                 5U
#define GPIOA_SPI1_MISO                6U
#define GPIOA_SPI1_MOSI                7U
#define GPIOA_RADIO_CS                 8U
#define GPIOA_USART1_TX                9U
#define GPIOA_USART1_RX                10U
#define GPIOA_USB_DM                   11U
#define GPIOA_USB_DP                   12U
#define GPIOA_SWDIO                    13U
#define GPIOA_SWCLK                    14U
#define GPIOA_PIN15                    15U

#define GPIOB_RADIO_IRQ                0U
#define GPIOB_GPS_RST                  1U
#define GPIOB_FLASH_RST                2U
#define GPIOB_PYROF_1                  3U
#define GPIOB_PYROF_2                  4U
#define GPIOB_PYROF_3                  5U
#define GPIOB_I2C1_SCL                 6U
#define GPIOB_I2C1_SDA                 7U
#define GPIOB_PIN8                     8U
#define GPIOB_MPU_CS                   9U
#define GPIOB_SPI2_SCK                 10U
#define GPIOB_PIN11                    11U
#define GPIOB_PIN12                    12U
#define GPIOB_MPU_IRQ                  13U
#define GPIOB_SPI2_MISO                14U
#define GPIOB_SPI2_MOSI                15U

#define GPIOC_PIN0                     0U
#define GPIOC_PIN1                     1U
#define GPIOC_PIN2                     2U
#define GPIOC_PIN3                     3U
#define GPIOC_PIN4                     4U
#define GPIOC_PIN5                     5U
#define GPIOC_PIN6                     6U
#define GPIOC_PIN7                     7U
#define GPIOC_PIN8                     8U
#define GPIOC_PIN9                     9U
#define GPIOC_PIN10                    10U
#define GPIOC_PIN11                    11U
#define GPIOC_PIN12                    12U
#define GPIOC_STAT_HBT                 13U
#define GPIOC_STAT_WRN                 14U
#define GPIOC_BEEP                     15U

#define GPIOD_PIN0                     0U
#define GPIOD_PIN1                     1U
#define GPIOD_PIN2                     2U
#define GPIOD_PIN3                     3U
#define GPIOD_PIN4                     4U
#define GPIOD_PIN5                     5U
#define GPIOD_PIN6                     6U
#define GPIOD_PIN7                     7U
#define GPIOD_PIN8                     8U
#define GPIOD_PIN9                     9U
#define GPIOD_PIN10                    10U
#define GPIOD_PIN11                    11U
#define GPIOD_PIN12                    12U
#define GPIOD_PIN13                    13U
#define GPIOD_PIN14                    14U
#define GPIOD_PIN15                    15U

#define GPIOE_PIN0                     0U
#define GPIOE_PIN1                     1U
#define GPIOE_PIN2                     2U
#define GPIOE_PIN3                     3U
#define GPIOE_PIN4                     4U
#define GPIOE_PIN5                     5U
#define GPIOE_PIN6                     6U
#define GPIOE_PIN7                     7U
#define GPIOE_PIN8                     8U
#define GPIOE_PIN9                     9U
#define GPIOE_PIN10                    10U
#define GPIOE_PIN11                    11U
#define GPIOE_PIN12                    12U
#define GPIOE_PIN13                    13U
#define GPIOE_PIN14                    14U
#define GPIOE_PIN15                    15U
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

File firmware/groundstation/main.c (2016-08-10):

/*
 * Martlet 3 Avionics - Radio Groundstation Blinker Test 
 *
 * N.B. Use of the SYSCFG_CFGR1 register is required to remap PA11/PA12
 *   
 */

#include "ch.h"
#include "hal.h"

/*
 * LEDs blinker thread, times are in milliseconds.
 */
static THD_WORKING_AREA(waThread1, 128);
static THD_FUNCTION(Thread1, arg) {

  (void)arg;
  chRegSetThreadName("blinker");
  while (true) {
    // Update LED pins
    palSetPad(GPIOA, GPIOA_STAT_HBT);
    palClearPad(GPIOA, GPIOA_STAT_WRN);
    chThdSleepMilliseconds(250);
    palSetPad(GPIOA, GPIOA_STAT_WRN);
    palClearPad(GPIOA, GPIOA_STAT_HBT);
    chThdSleepMilliseconds(250);
  }
}

/*
 * Application entry point.
 */
int main(void) {

  /*
   * System initializations.
   * - HAL initialization, this also initializes the configured device drivers
   *   and performs the board-specific initializations.
   * - Kernel initialization, the main() function becomes a thread and the
   *   RTOS is active.
   */
  halInit();
  chSysInit();

  /*
   * Creates the blinker thread.
   */
  chThdCreateStatic(waThread1, sizeof(waThread1), NORMALPRIO, Thread1, NULL);

  
  /*
   * Normal main() thread activity, in this demo it does nothing.
   */
  while (true) {
	chThdSleepMilliseconds(1000);
  }
}

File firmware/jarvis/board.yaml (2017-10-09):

name: Jarvis Flight Computer
lsefreq: 0
hsefreq: 26000000
voltage: 3.0
mcutype: STM32F411xE
default: input, pushpull, starthigh, pullup, highspeed
pins:
    SWDIO:      pa13, af0
    SWCLK:      pa14, pulldown, af0
    
    STAT_HBT:   pc13, output, pushpull, startlow
    STAT_WRN:   pc14, output, pushpull, startlow
    
    BEEP:       pc15, output, pushpull, startlow, pulldown
    
    BAT_MON:    pa3, analog, floating
    
    PYROS_1:    pa0, output, pushpull, startlow
    PYROS_2:    pa1, output, pushpull, startlow
    PYROS_3:    pa2, output, pushpull, startlow
    
    PYROF_1:    pb3, output, pushpull, startlow
    PYROF_2:    pb4, output, pushpull, startlow
    PYROF_3:    pb5, output, pushpull, startlow
    
    FLASH_CS:   pa4, output, pushpull
    RADIO_CS:   pa8, output, pushpull
    
    SPI1_MOSI:  pa7, af5
    SPI1_MISO:  pa6, af5
    SPI1_SCK:   pa5, af5
    
    USART1_TX:  pa9, af7
    USART1_RX:  pa10, af7
    
    USB_DM:     pa11, af10
    USB_DP:     pa12, af10
    
    RADIO_IRQ:  pb0, input
    GPS_RST:    pb1, output, pushpull, pullup
    FLASH_RST:  pb2, output, pushpull, pullup
    
    I2C1_SDA:   pb7, af4, opendrain
    I2C1_SCL:   pb6, af4, opendrain
    
    MPU_CS:     pb9, output, pushpull
    MPU_IRQ:    pb13, input
    
    SPI2_MOSI:  pb15, af5
    SPI2_MISO:  pb14, af5
    SPI2_SCK:   pb10, af5
    

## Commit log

2016-03-21 Completed Boost Converter
    [Jarvis.kicad_pcb, Jarvis.sch]
2016-03-24 Added External Connectors & STM32F411CxUx with peripherals configured
    [Jarvis.sch]
2016-03-25 Added Radio & Barometer
    [Jarvis.sch]
2016-03-28 Progressed Schematic
    [Jarvis.sch]
2016-03-29 BOM near completion
    [Ground Station.kicad_pcb, Ground Station.sch, Jarvis.kicad_pcb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]
2016-03-30 Started PCB Layout
    [Jarvis.kicad_pcb, Jarvis.sch]
2016-03-31 Schematic Complete
    [Jarvis.kicad_pcb, Jarvis.sch]
2016-03-31 Added Testpoints
    [Jarvis.kicad_pcb, Jarvis.sch]
2016-04-01 Added mounts & placed ecternal connectors
    [Jarvis.kicad_pcb]
2016-04-04 Routed PSU
    [Jarvis.kicad_pcb, Jarvis.sch]
2016-04-06 Replaced SD Card with 16MB Flash and started placment
    [Jarvis.kicad_pcb, Jarvis.sch]
2016-04-08 Routing progress
    [Jarvis.kicad_pcb, Jarvis.sch]
2016-04-09 Continued Layout
    [Jarvis.kicad_pcb, Jarvis.sch]
2016-04-13 Continued PCB
    [Jarvis.kicad_pcb, Jarvis.sch]
2016-04-18 Ready to Check Footprints
    [Jarvis.kicad_pcb, Jarvis.sch]
2016-04-19 Finished PCB
    [Jarvis.kicad_pcb]
2016-04-19 Started Ground Station Footprints
    [Ground Station.kicad_pcb, Ground Station.sch]
2016-04-21 Finished Ground Station Schemnatic
    [Ground Station.kicad_pcb, Ground Station.sch]
2016-04-21 Generated pdf
    [Ground Station.kicad_pcb, Ground Station.sch]
2016-04-23 Finished ground station
    [Ground Station.kicad_pcb, Ground Station.sch, Jarvis.kicad_pcb]
2016-05-07 Checked all Footprints
    [Ground Station.kicad_pcb, Ground Station.sch, GroundStation.csv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]
2016-05-08 All checked and panel completed
    [Ground Station.kicad_pcb, Jarvis.kicad_pcb, panel.kicad_pcb]
2016-05-08 Modified tolerence
    [Ground Station.kicad_pcb, Jarvis.kicad_pcb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]
2016-05-15 Generated gerbers
    [Jarvis.gbl, Jarvis.gbo, Jarvis.gbp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]
2016-06-21 Modified radio circuit to 868MHz and generated stickerBOM
    [Ground Station.sch, GroundStation.csv, Jarvis.csv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]
2016-06-25 Corrected Radio Passives in Ground Station
    [Ground Station.kicad_pcb, Ground Station.sch, Jarvis.kicad_pcb]
2016-06-25 Tidy up before final assembly
    [Ground Station.sch, Jarvis.kicad_pcb]
2016-08-10 LED now blinks
2016-09-03 Added board.yaml
2016-12-05 Updated board.h
    [Jarvis.sch]
2016-12-06 DMA and CLK config
2017-10-09 started barometer driver
    [Jarvis.sch]
2017-10-10 i2c driver trouble
2017-10-10 pressure sensor works
2017-10-12 added ADP1607 footprint to local library
